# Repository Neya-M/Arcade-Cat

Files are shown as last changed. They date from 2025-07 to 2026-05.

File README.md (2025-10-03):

# Arcade Cat



This is a claw machine where the claw is actually a cat! It will be pretty big, 2x2x2 feet plus some area at the bottom for the prize hole and controls.

Why did I make this? Every year my school has a craft fair and I never sell much ;-; I was wondering "how am I supposed to sell stuff if everyone is making the _same exact thing_ as me??" Well I was already ok in hardware so I decided to make a claw machine!! :D

## Wiring:


## BOM:

|Name|Link|
|-|-|
|1x Joystick|https://www.seeedstudio.com/Grove-Thumb-Joystick.html|
|600mm of Aluminum Extrusion|https://a.co/d/1keCCWv|
|1x Button|https://a.co/d/bO5OvMs|
|4x 24x24" Sheet of Plywood|https://www.lowes.com/pd/1-4-in-Birch-Plywood-Application-as-2-x-2/1000066171|
|Gear and rack|https://www.thingiverse.com/thing:3444515|
|2x Servo Motors|https://a.co/d/iEjD7D2|
|4x 24x24" Acrylic|too expensive, will use plastic wrap instead :pf:|
|2x Nema 17 Motors|https://a.co/d/5XWT3yt|
|Glue (likely epoxy)|no need for glue anymore :pf:|
|3x Motor Drivers (TMC2209)|https://a.co/d/hs2fbK3|
|Spool|will be made out of cardboard|
|1x Orpheus pi Pico|https://www.adafruit.com/product/4864|
|1x LED strip|https://www.aliexpress.us/item/2255800625645532.html|
|2x Potentiometer|https://www.aliexpress.us/item/3256808151995054.html|

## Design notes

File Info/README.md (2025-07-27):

# Claw Machine



This is a claw machine where the claw is actually a cat! It will be pretty big, 2x2x2 feet plus some area at the bottom for the prize hole and controls.

Why did I make this? Every year my school has a craft fair and I never sell much ;-; I was wondering "how am I supposed to sell stuff if everyone is making the _same exact thing_ as me??" Well I was already ok in hardware so I decided to make a claw machine!! :D

## Wiring:


## BOM:

|Name|Link|
|-|-|
|1x Joystick|https://www.seeedstudio.com/Grove-Thumb-Joystick.html|
|600mm of Aluminum Extrusion|https://a.co/d/1keCCWv|
|1x Button|https://a.co/d/ghnM8m8|
|4x 24x24" Sheet of Plywood|get from local store|
|Gear and rack|https://www.thingiverse.com/thing:3444515|
|2x Servo Motors|https://a.co/d/1wKk91z (pack of 4)|
|4x 24x24" Acrylic|get from local store|
|2x Nema 17 Motors|https://a.co/d/hWB0tbz|
|Glue (likely epoxy)|get from local store|
|3x Motor Drivers (TMC2209)|https://www.aliexpress.us/item/3256809236175649.html OR https://a.co/d/hs2fbK3|
|Spool|will be made out of cardboard|
|1x Orpheus Pico|will get from SoM https://summer.hackclub.com/|
|1x LED strip|https://www.aliexpress.us/item/2255800625645532.html|
|2x Potentiometer|https://www.aliexpress.us/item/3256806569463411.html|

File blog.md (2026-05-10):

# Claw machine
This was a difficult project, and one of my first hardware projects. I started it along with my hackpad in summer of 2025 and it has been in the building process on and off since then.

To start, i ordered my parts, and that took a long time too because all the products would disappear from the websites before i could finalize my BOM. But once i had that done...

I cut the wood and assembled the base. I learned that thin wood is not such a good building material because all the little screws poked out the sides. The supports were also thin and flimsy so i swapped them out later on.

I then tried to get each part to respond to the raspberry pi, and i got the joystick to send directions, the button to give an on/off signal, the servos turned and the LEDs lit up. But i had no idea how motors and motor drivers worked.

Turns out, I needed 12 volts and 1-2 amps, which definitely not going to be battery powered or drawn from my pi. I had a brick to connect to the wall but no adapter to my motors. So i just ignored the motors.

Then i fried my raspberry pi trying to power the motors, luckily i got a new one from a friend.

Then i learned that aluminum extrusions aren't for sliding and i needed belts and gears. Soooo i couldn't get the axes to work ;-;

I did replace the supports with stronger ones and i swapped out the screws for nuts and bolts. turns out nuts and bolts are really strong!
I also got my claw to finally work. Turns out that 360 servos means that it rotates continuously, rather than to an angle. 
I found out that a lot of my problems were from voltage mismatches, like my servos and joystick needed 5v rather than the 3v that i was connecting them to.

I knew so little about hardware and structural design but i'm glad i went for it and i hope i can continue this soon :)

### Parts needed
- adapter to connect motor drivers to wall
- belts
- step down module (so that i can also power the 5v stuff off of wall

### Pictures :)



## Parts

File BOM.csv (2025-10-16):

Name | Link | Price
1x Joystick | https://www.aliexpress.us/item/3256809848658792.html | $3.98
600mm of Aluminum Extrusion | https://a.co/d/1keCCWv | $9.99 + 6.99
1x Button | https://www.aliexpress.us/item/3256806392621033.html | $3.75
4x 24x24" Sheet of Plywood | https://www.lowes.com/pd/1-4-in-Birch-Plywood-Application-as-2-x-2/1000066171 | $11.12
Gear and rack | https://www.thingiverse.com/thing:3444515 | N/A
2x Servo Motors | https://www.aliexpress.us/item/3256806385982254.html | $2.56
4x 24x24" Acrylic | too expensive, will use plastic wrap instead :pf: | N/A
2x Nema 17 Motors | https://www.aliexpress.us/item/3256808273084374.html and https://a.co/d/eWfPTz6 | $17.53 + 6.99 shipping + 1.36 tax
Glue (likely epoxy) | no need for glue anymore :pf: | N/A
3x Motor Drivers (TMC2209) | https://www.aliexpress.us/item/3256808770530741.html | $7.85
Spool | will be made out of cardboard | N/A
1x pi Pico | https://www.aliexpress.us/item/3256808528593259.html | $4.55
1x LED strip | https://www.aliexpress.us/item/2255800625645532.html | $5.82 + $3.26 shipping
2x Potentiometer | https://www.aliexpress.us/item/3256808151995054.html | $0.83 + $4.90 shipping
Total Price |  | $140.79

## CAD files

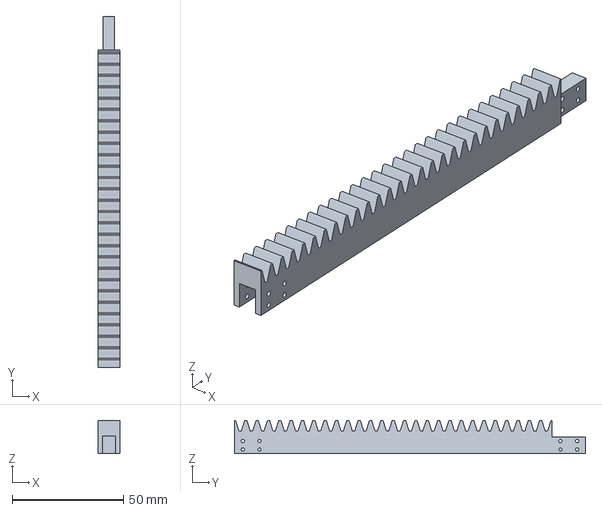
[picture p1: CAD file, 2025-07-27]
CAD (3mf)/Rack.3mf
10.0 x 157.8 x 15.0 mm

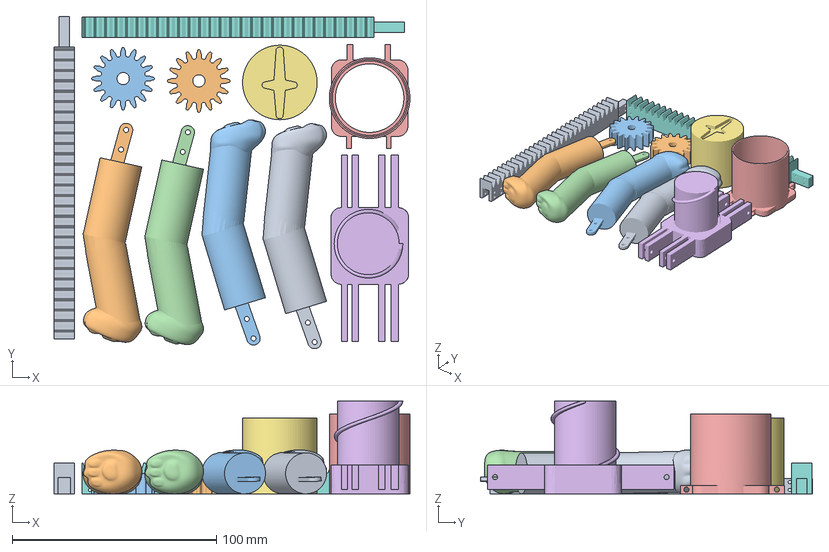
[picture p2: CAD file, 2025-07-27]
CAD (3mf)/All_parts_except_body.3mf
174.2 x 162.7 x 45.3 mm
Assembly 2 1.stl x 2
Assembly 2.stl x 2
thing.stl
Assembly 2 copy.stl
SG90 - Micro Servo 9g - Tower Pro v6 - Part 3.stl
rackV1 - Part 1.stl x 2
pinion_spur_16t - Part 1.stl x 2

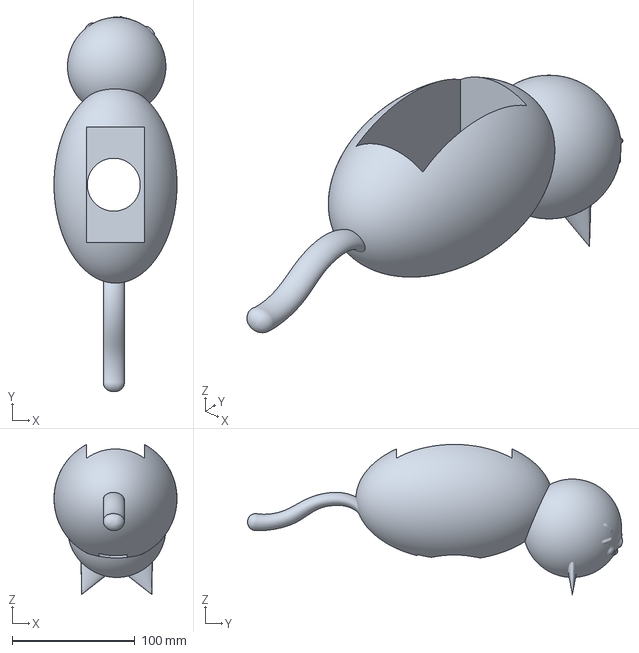
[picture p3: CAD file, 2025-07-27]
CAD (3mf)/Body.3mf
100.0 x 304.9 x 122.0 mm

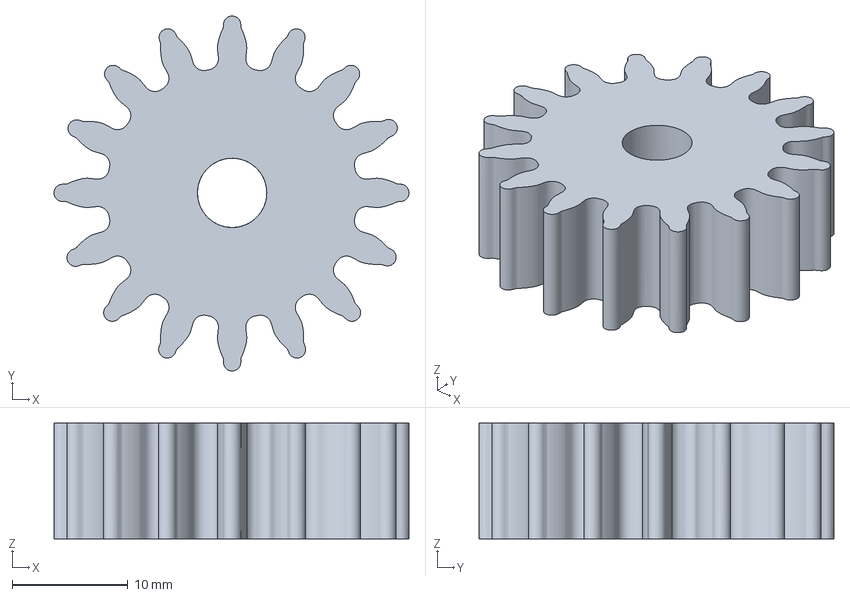
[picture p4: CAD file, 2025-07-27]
CAD (3mf)/Gear.3mf
30.7 x 30.7 x 10.0 mm

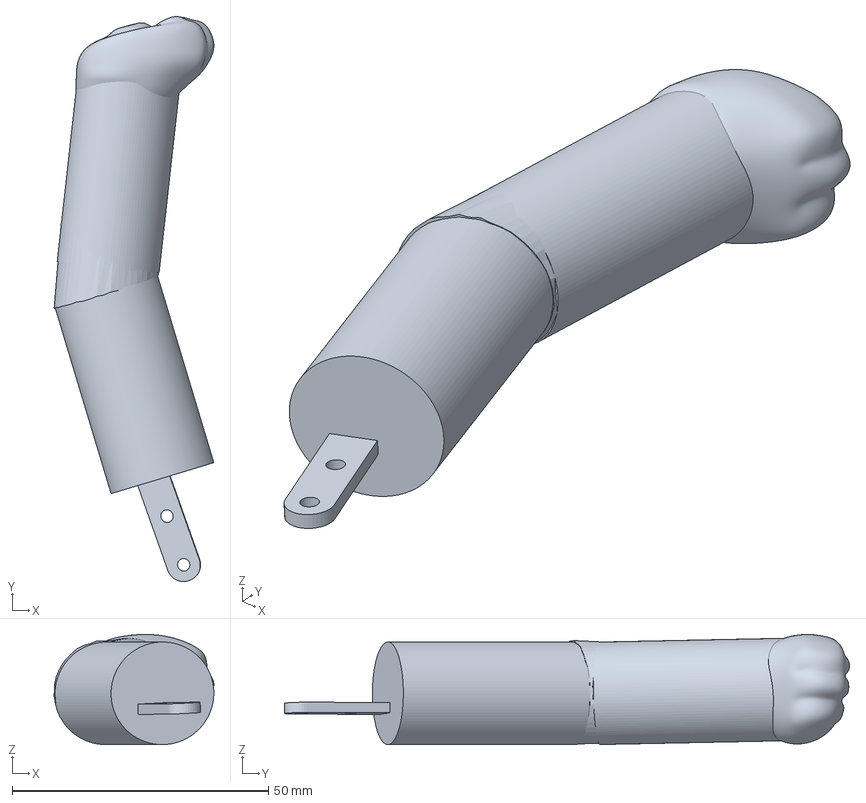
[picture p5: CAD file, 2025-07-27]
CAD (3mf)/Front_leg.3mf
31.2 x 110.2 x 21.5 mm

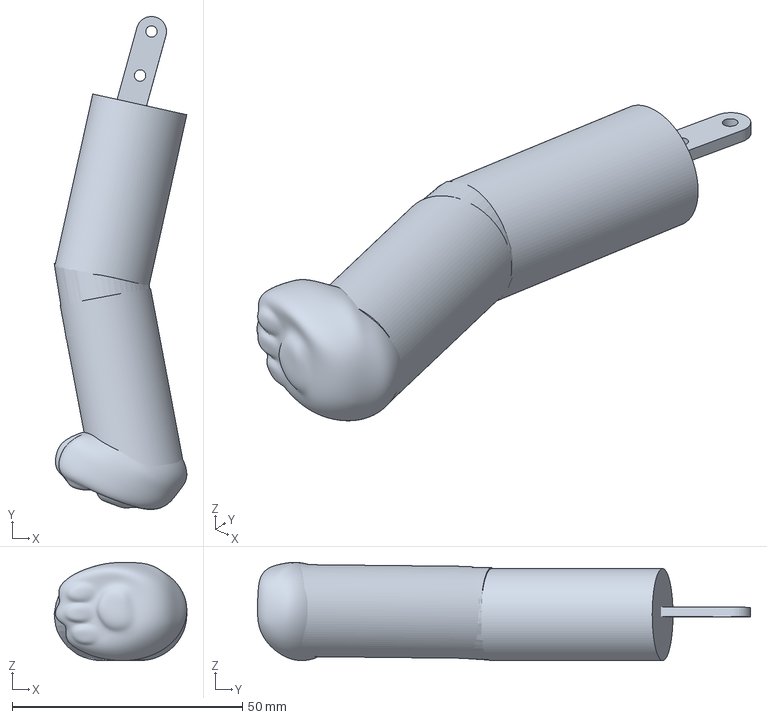
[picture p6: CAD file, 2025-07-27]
CAD (3mf)/Back_leg.3mf
28.8 x 107.1 x 21.3 mm

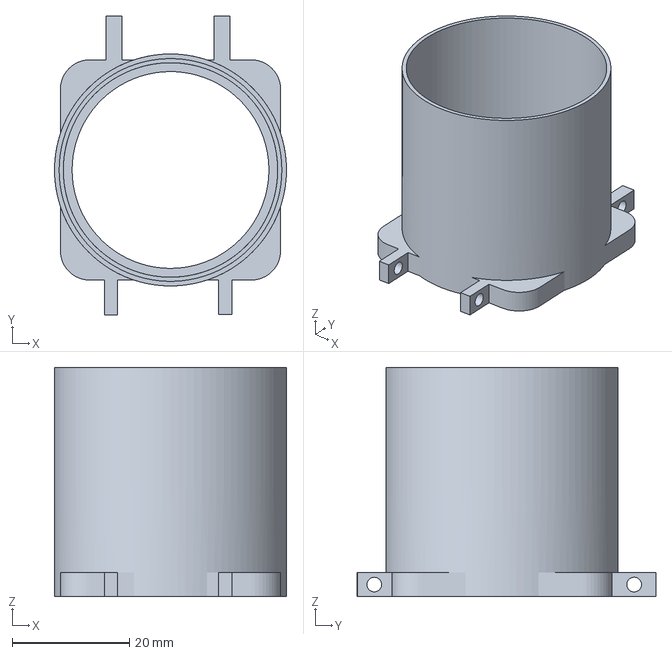
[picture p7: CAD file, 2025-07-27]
CAD (3mf)/Screw_case.3mf
39.5 x 50.9 x 39.0 mm

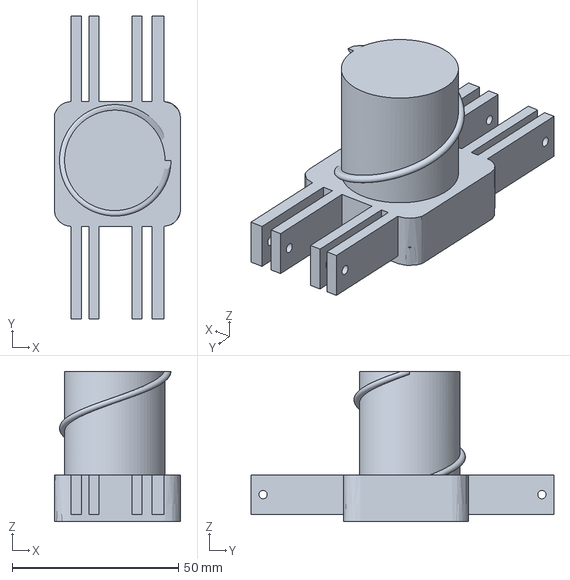
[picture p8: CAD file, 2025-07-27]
CAD (3mf)/Screw2.3mf
38.0 x 91.2 x 45.3 mm

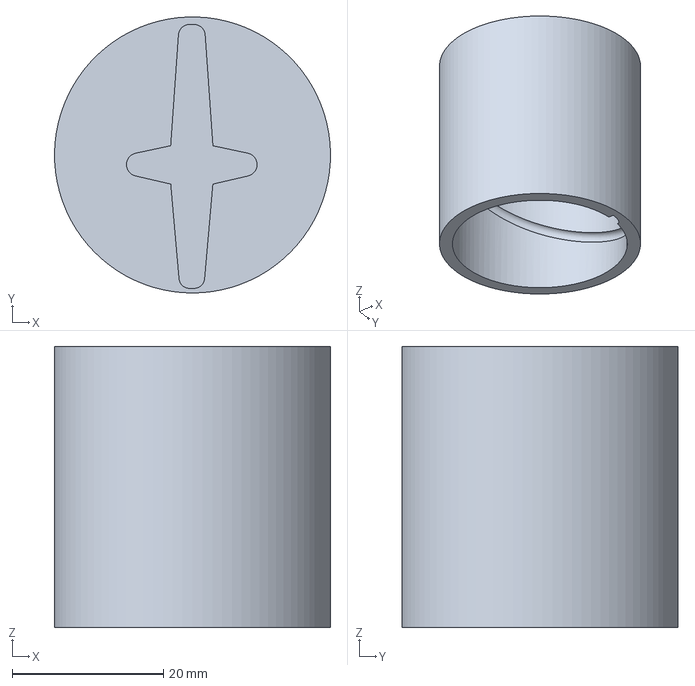
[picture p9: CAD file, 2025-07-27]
CAD (3mf)/Screw1.3mf
36.5 x 36.5 x 37.2 mm

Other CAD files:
CAD (stl)/Gear.stl
CAD (stl)/Rack.stl
CAD (stl)/Screw1.stl
CAD (stl)/Screw2.stl
CAD (stl)/Screw_case.stl
CAD/backleg.stl

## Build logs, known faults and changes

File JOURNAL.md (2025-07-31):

---
title: "Claw Machine"
author: "Neya"
description: "Just a claw machine"
created at: "2025-06-4"
time spent overall: "14h"
---

# June 4th: Sketched the motor system

I made a sketch of where the motors would go so I have an idea of how it will work (oh no its low quality 😭)



**Total time spent: ~15m**

# July 21st: completed the diagrams of motor systems

I finally finished the other YSWSes so I have time for this, here are some much more detailed (yet still very scrappy) sketches of my motor system:



This is a diagram of where the x, y, and z axes are.



The left side of the y axis is a gear rack. a gear (red) on a stepper motor (blue) uses this to move the x axis forward and backward. The other side of the y axis is an aluminum extrusion (green), which supports the x axis while still letting it slide back and forth.



The x axis is a wooden board with a slot cut out of it. This slot lets the cord of the z axis (not shown) through. It is attatched to the stepper motor from the previous image so it can move along the y axis. There is another stepper motor (blue) on the x axis that also uses a gear and rack to move along t
he x axis. This stepper is glued to the z controls as shown in the next images.




This is the z axis. it is a spool with a cord (purple) that moves the claw up and down. It uses a servo to turn the spool, and if more revolutions are needed, I can add a gear box. This servo is connected to the x axis stepper motor that moves it left and right.



The claw is a cat that picks up prizes with its paws. Servo #2 turns a screw-like system (shown in purple and pink) which moves it up, closing the claw as shown in the diagram.

**Total time spent: ~1h**

# July 21-22nd: CAD

Here is a CAD model of all the pieces in the claw. CAD takes so loooooong :'(





**Total time spent: ~6h**

# July 22-23: Parts

I picked out the parts I need for this and added links. 



**Total time spent: ~2.5h**

# July 23: Wooden structure

Here's how I'll cut the 4 wood pieces:



The yellow and pink squares will be cut out in order to let prizes through. Diagrams of how these pieces will be attatched:




**Total time spent: ~30m**

# July 24: Firmware draft

Finished the first draft of the firmware but I'll need to have the actual hardware to test it

Screenshots of code are boring so no picture for this one :')

**Total time spent: ~1h**

# July 25: CAD fixes

fixed up the cad model so you only need 360 degrees to move the claw.

Before:



After:



There's also a hole for the servo now.


**Total time spent: ~1h**

# July 25-26: Wiring

made the wiring diagram and prepared this project for shipping!



**Total time spent: ~1.5h**

# July 27: 3mf, BOM, and Credits

I added the 3mf files and added credits for cad that wasn't mine







⬆

I hope the BOM is supposed to look like this

**Total time spent: ~1.5 hours**

# July 31: Fix BOM

I redid the BOM because it turns out it wasn't supposed to look like that. :(



But now I have this nice one :D

**Total time spent: ~15m**

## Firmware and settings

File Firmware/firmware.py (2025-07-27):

from machine import Pin, ADC
import utime
from servo import Servo
from neopixel import Neopixel
import random

NUM_LEDS = 30
PIXEL_PIN = 0  # switch to real gpio pin
pixels = Neopixel(NUM_LEDS, 0, PIXEL_PIN, "RGBW")


# servo 1 needs to control the z spool, will go to 360 when button is pressed,
# wait a second and then go back to 0
servo1 = Servo(0)
# servo 2 needs to control the claw, so same movement as servo 1 (may be
# reversed)
servo2 = Servo(1)
# stepper 1 will run one way when joystick x is positive and the other way when
# negative
step1 = Pin(2, Pin.OUT)
dir1 = Pin(3, Pin.OUT)
# stepper 2 will run same as stepper 1 except for the y axis
step2 = Pin(4, Pin.OUT)
dir2 = Pin(5, Pin.OUT)
# map of where the claw is so motors don't go too far
# 0, 0 is the prize hole
xymap = [0, 0]
# placeholders for now
xlimit = 24
ylimit = 24

xAxis = ADC(Pin(26))
yAxis = ADC(Pin(27))
joystick_btn = Pin(16, Pin.IN, Pin.PULL_UP)
button = Pin(17, Pin.IN, Pin.PULL_UP)


def step_once(step_pin, dir_pin, direction, delay=0.001):
    dir_pin.value(direction)
    step_pin.high()
    utime.sleep(delay)
    step_pin.low()
    utime.sleep(delay)


def collect_prize(serv_1, serv_2):
    serv_1.move(360)  # spool
    serv_2.move(360)  # claw
    utime.sleep(0.5)
    serv_1.move(0)
    serv_2.move(0)


def goto_xy(stepA, stepB, dirA, dirB):
    print("ok")
    # this will depend heavily on the speed of the motors and the size of the
    # machine. Will finish later


def update_neopixels():
    colors = [[50, 0, 0, 25],  # pink
              [0, 20, 0, 25],  # light green
              [5, 0, 50, 25],  # blue
              [20, 25, 0, 25],  # yellow
              [0, 0, 5, 30]]  # white
    pixels.fill((colors[random.randint(1, 5)]))  # r, g, b, w
    pixels.show()


while True:
    # joystick
    x = xAxis.read_u16()
    y = yAxis.read_u16()
    btn_jstick = joystick_btn.value()
    btn = button.value()

    if btn == 1:
        collect_prize(servo1, servo2)
        goto_xy(step1, step2, dir1, dir2, 0, 0)
    if x > 0:
        step_once(step1, dir1, 1)
    elif x < 0:
        step_once(step1, dir1, 0)
    if y > 0:
        step_once(step2, dir2, 1)
    elif y < 0:
        step_once(step2, dir2, 0)
    # angle1 = int((x / 65535) * 360)
    # angle2 = int((y / 65535) * 360)

    utime.sleep(0.01)

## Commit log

2025-07-26 CAD files
    [body.stl, cat head.stl, otherscrew.stl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]
2025-07-26 add to folder
    [backleg.stl]
2025-07-26 add cad
    [otherscrew.stl, screw.stl, thing.stl]
2025-07-27 3mf files and credits
    [All_parts_except_body.3mf, Back_leg.3mf, Body.3mf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]
2025-07-31 Add fixed BOM
    [BOM.csv]
